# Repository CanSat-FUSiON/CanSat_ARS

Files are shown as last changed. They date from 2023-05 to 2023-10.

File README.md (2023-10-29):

# CanSat_ARS-1.00

**Present Version : ARS-1.00**
誰かが個人単位でリファクタリングやデバッグしたら+0.01，ミッションぐるみで大型アップデートをしたら+1.00して小数部切り捨て．
編集したら更新すること
ToDoはここに記すと管理しやすい：https://github.com/orgs/CanSat-FUSiON/projects/5/views/1?layout=board

## ディレクトリ説明
|ディレクトリ名|説明|
|----|----|
|Design-Data|CanSatの設計データが格納されています．CanSatを自分の好きなようにアレンジする場合にはこちらのディレクトリを操作してください．|
|Operation-Guide|CanSatの保守運用に関するデータが格納されています．機器の組立てと運用を行う場合はこのディレクトリのみ覗けば大丈夫です．|

## 命名規則
ディレクトリ名は原則，頭文字のみ大文字(複数単語は"-"で接続)
ファイル名は小文字統一

マークダウンファイルはGitHub直下のみ`README.md`とし(本ファイル)，それ以下の階層ではファイルの内容に従って命名する．
例）`./Design-Data/Hardware/`におけるハードウェア機器の構成を説明するためのマークダウンファイルは`ハードウェア機器の構成.md`

## コーディング規則
開発に使う言語としてpythonを用いる．
ただし，OBCの変更や機能拡張に伴い要求が変わる場合その限りではない．
pythonにおけるコーディング規約として，[pep8](https://pep8-ja.readthedocs.io/ja/latest/)にしたがう．

## ブランチの使い方
大会の出場の途中などで頻繁な更新が想定される際は，`main`の代理となる別な開発ブランチを設けること．
その場合，審査書提出後や，大会期間が終了時など，変更が安定した時点で開発ブランチを`main`にマージすること．
例）Mission4の開発期間中→`dev-m4`などと名付け暫定的な`main`の代わりとして用いる．

## コミットメッセージ
コミットメッセージは以下の4種類から適切なものを選び **(作業対象)+(: )+(作業分類)+(半角スペース)+(作業内容)** と書く．
例）`zero: Add telecomunication driver`
|作業分類|説明|
|----|-----|
|fix|バグ修正|
|add|新規(ファイル)機能追加|
|update|機能修正(バグではない)|
|remove|削除(ファイル)|

※（参考）https://qiita.com/itosho/items/9565c6ad2ffc24c09364

## ライセンス
This repository is released under the MIT License, see LICENSE.txt.

このリポジトリはMITライセンスのもとで公開されている． 'LISENCE.txt'を参照．

## バージョン管理
|Ver.|内容|
|----|----|
|1.00|Mission2終了時点の完成形CanSat|
|||

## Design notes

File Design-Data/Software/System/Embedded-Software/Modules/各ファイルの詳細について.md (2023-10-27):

# Modules
CanSatの組み込みソフトウェアに使うModuleをまとめるディレクトリです。

## ファイルの説明
|ファイル名|説明|
|----|-----|
|camerarun.py|画像処理走行のクラスを定義しているファイル|
|communication.py|LoRa通信のクラスを定義しているファイル|
|gpsrunner.py|GPS走行のクラスを定義しているファイル|
|landingdetecter.py|着地判定のクラスを定義しているファイル|
|logs.py|あらゆるログを記録するためのクラスを定義しているファイル|
|longsleep.py|走行前のスリープを制御するクラスを定義しているファイル|
|mdlreddetect.py|赤色を検出する関数が定義されているファイル|
|motor.py|CanSatの走行を統括するクラスが定義されているファイル|
|runpattern.py|CanSatの走行パターンの関数を定義しているファイル|
|sensor.py|GPSや9軸センサなどの値を取得するクラスを定義しているファイル|
|stack.py|様々な方法でスタックを判定するクラスが定義されているファイル|
|step.py|GPS走行中、ループの中で、それぞれの判定が設定されたインターバル通りに実行されるよう計測するクラスを定義したファイル|
|sleeptime.txt|スリープの設定時間が記録されるテキストファイル|

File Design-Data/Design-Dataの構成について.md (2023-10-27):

# Design-Data

ARSモデルの設計データを記載する．
現在のディレクトリは以下のように分けられる．
|フォルダ名|説明|
|----|----|
|Mechanic|機体構造や試験によって判明した物理特性に関するデータを記載する．|
|Hardware|組み込みハードウェア分野についての設計データを集める．マイコンとセンサ，アクチュエータなどの電気的な接続やPCBデータなど．|
|Software|組み込みソフトウェアや画像処理分野の設計データを集める．|

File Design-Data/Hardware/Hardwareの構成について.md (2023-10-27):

# Hardware
FUSiONのCanSat Model ARS系統のハードウェア設計

## ピンアサイン


更新する際は[こちらのスプレッドシート](https://docs.google.com/spreadsheets/d/1eQN7OE-Z9ALaf2SgiwYws5UZOM_eGH8C7UVVMnbFOFw/edit#gid=0)をコピーしてスクリーンショットを添付して下さい  

## 部品リスト
用いた代表的な部品は以下の通り．
具体的な型番などは別ファイルで示す．
|部品名|用途|
|----|----|
|温湿度気圧センサ|気温・気圧から高度を測定|
|9軸センサ|自身の向きの確認．及び転倒やスタック検知|
|GPSセンサ|自身の座標の確認．|
|モーター|走行やスタックからの脱出．|

以下に詳細な部品リストを表示する

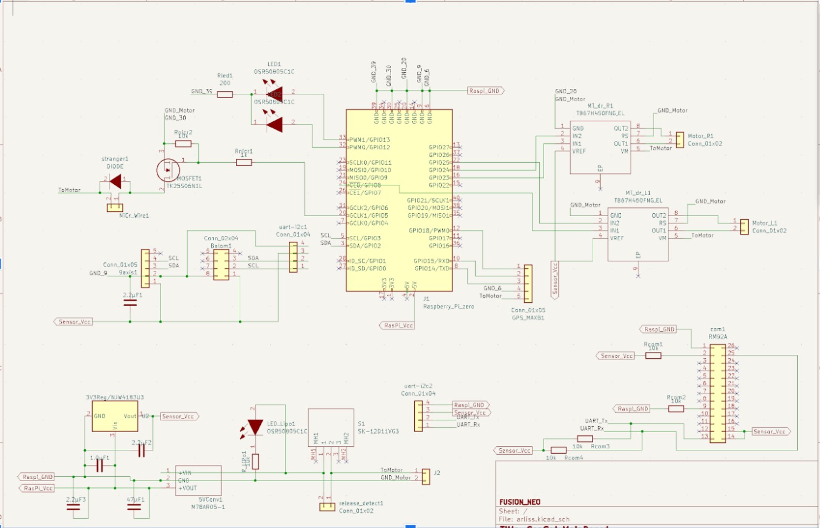
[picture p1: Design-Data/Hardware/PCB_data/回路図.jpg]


|名前|型番|用途|数|
|----|----|----|----|
|||||

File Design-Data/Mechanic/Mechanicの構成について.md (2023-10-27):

# Mechanic
CanSatをなす部品のCadデータを格納されている。
".f3z"はダウンロードした上でfusion360内でファイルを選び展開する。

## ディレクトリ/ファイルの説明
|ディレクトリ/ファイル名|説明|
|----|-----|
|buildup.f3z|すべての部品が統合されているcadファイル|
|parts|部品のcadデータが格納されたファイル|

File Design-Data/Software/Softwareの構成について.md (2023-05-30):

# Software
組込みソフトウェア，その他画像処理などのソフトウェアに関して記す．

## ディレクトリ説明
|ディレクトリ名|説明|
|----|-----|
|System|最終的に使用したプログラム|
|Interface-Test|複数の機能を連続して動かす際のテストに使うプログラム|
|Function-Test|機能単位のテストに使うプログラム|
|Component-Test|部品単位のテストに使うプログラム|

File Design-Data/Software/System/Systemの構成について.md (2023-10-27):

# System
マザーボードに組み込むデータと通信に使うデータを格納している。

## ディレクトリ/ファイルの説明
|ディレクトリ/ファイル名|説明|
|----|-----|
|Embedded-software|マザーボードに組み込むプログラムが格納されたディレクトリ|
|LoRa-software|通信機器に組み込むプログラムが格納されたディレクトリ|

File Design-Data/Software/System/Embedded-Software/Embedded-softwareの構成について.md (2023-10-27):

# Embedded-software
走行で実際に使用するプログラムとそれらのModuleをまとめるディレクトリです。
このディレクトリ上でmain.pyを実行すると、統合された組み込みプログラムが実行され、
打ち上げ開始からの一連の動作が始まります。

## ディレクトリ/ファイルの説明
|ディレクトリ/ファイル名|説明|
|----|-----|
|Modules|各種クラスを定義したプログラムをまとめたディレクトリ|
|main.py|mainとして実行するプログラム|

## 注意
- sleeptime.txtの数値を確認する。
    - この数値が-1だと、すぐに落下判定のフェーズに入る。実行からsleepする時間はこの数値を変更することで設定できる。
    - 数値はmain.pyの実行ごとに変更されていくため、毎回チェックする必要がある。
- 今後追加します。

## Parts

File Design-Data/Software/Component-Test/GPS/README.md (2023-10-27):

# 説明
GPS用の動作試験用プログラムです．

## 使い方
terminalからGPSモジュールをインストールしてください
>$pip install GPS3

UARTピン(TX:GPIO14，RX:GPIO15)に接続したのち，GPS.pyを実行してください．

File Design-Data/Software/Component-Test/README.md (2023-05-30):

# Component-Test

組込みモジュールそれぞれのテストをするためのディレクトリです．

## 組み込み部品リスト
|部品名|型番号|
|----|----|
|温湿度気圧センサ|[LPS25HB](https://akizukidenshi.com/catalog/g/gK-13460/)|
|9軸センサ|[BNO055](https://akizukidenshi.com/catalog/g/gK-16996/)|
|GNSSモジュール|[現行版](https://akizukidenshi.com/catalog/g/gK-13849/)|
|通信モジュール|[RM-92A](https://www.green-house.co.jp/products/rm-92as/)|

# ファイル説明
|ファイル名|説明|
|----|----|
|lps25hb_data.py|温湿度気圧センサlps25hbからそれぞれの情報を取得するためのプログラム|
|bno055_data.py|9軸センサbno055からそれぞれの軸のデータを取得するためのプログラム|
|maxb_data.py|GNSSモジュールから3次元座標と時刻を取得するためのプログラム|

# 関連ライブラリ
|ライブラリ名|説明|
|----|----|
|LPS25HB.py|LPS25HB動作用のライブラリ|
|adafruit_bno055.py|adafruit社製BNO055動作用ライブラリ|
|......|......|

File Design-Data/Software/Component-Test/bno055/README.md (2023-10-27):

# 説明
bno055.pyを書き込んだ後に，bno055TEST.pyを動作してください．

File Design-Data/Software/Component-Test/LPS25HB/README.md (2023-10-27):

# 説明
気温・気圧センサであるLPS25HBの動作プログラムです．
LPS25HB.pyというモジュールを書き込み，LPS25HBTEST.pyで動作させてください．

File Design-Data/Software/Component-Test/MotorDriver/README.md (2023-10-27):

# 説明
モーターの試運転用プログラムです．

## ピンアサイン
右前転|25
右後転|8
左前転|23
左後転|24

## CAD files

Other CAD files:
Design-Data/Hardware/PCB_data/pico_greenhouse/LIB_PICO/PICO/Allegro/pico.psm
Design-Data/Hardware/PCB_data/pico_greenhouse/LIB_PICO/PICO/DEHDL/pico/chips/chips.prt
Design-Data/Mechanic/Assemblies/GYSFDMAXB.f3d
Design-Data/Mechanic/Assemblies/bearingholder.f3d
Design-Data/Mechanic/Assemblies/coupling.f3d
Design-Data/Mechanic/Assemblies/motorholder.f3d
Design-Data/Mechanic/Assemblies/plate1.f3d
Design-Data/Mechanic/Assemblies/plate2.f3d
Design-Data/Mechanic/Assemblies/plate3.f3d
Design-Data/Mechanic/Assemblies/ripobattery.f3d
Design-Data/Mechanic/Assemblies/shaft.f3d
Design-Data/Mechanic/Assemblies/shaftholder.f3d
Design-Data/Mechanic/Assemblies/spacer_20mm.f3d
Design-Data/Mechanic/Assemblies/spacer_30mm.f3d
Design-Data/Mechanic/Assemblies/stabilizer.f3d
Design-Data/Mechanic/Assemblies/substrate1.f3d
Design-Data/Mechanic/Assemblies/substrate2.f3d
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

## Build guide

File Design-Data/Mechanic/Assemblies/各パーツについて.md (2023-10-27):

# Parts
CanSatをなす部品が個別に格納されている。
拡張子が".f3d"のためダウンロードした上、fusion360で展開する。

## ディレクトリ/ファイルの説明

以下にファイル名と内容についてまとめた。プリント欄が〇となっているものは3Dプリンターで制作するもの、✕となっているものは購入・発注・製作するものである。

|ファイル名|説明|プリントの有無|データシート|購入リンク|
|----|----|----|----|----|
|plate1.f3d|CanSat上層部のデータ|〇|-|-|
|plate2.f3d|CanSat中層部のデータ|〇|-|-|
|plate3.f3d|CanSat下層部のデータ|〇|-|-|
|substrate1.f3d|raspberryPi 0を載せた基板データ|✕|[here](./../../../Hardware/)|-|
|substrate2.f3d|9軸センサーを載せた基板データ|✕|[here](./../../../Hardware/)|-|
|substrate3.f3d|RaspberryPi Picoを載せた基板データ|✕|[here](./../../../Hardware/)|-|
|GYSFDMAXB.f3d|GPSセンサーのデータ|✕|[here](https://akizukidenshi.com/download/ds/akizuki/AE-GPS_manual_r1.06_s.pdf)|[here](https://akizukidenshi.com/catalog/g/gK-13849/)*|
|tire.f3d|タイヤのデータ|〇|-|-|
|wheel.f3d|ホイール部分のデータ|〇|-|-|
|shaft.f3d|シャフトのデータ|✕|-|-|
|shaftholder.f3d|シャフトとホイールをつなげるシャフトホルダーのデータ|✕|[here](https://jp.misumi-ec.com/pdf/fa/2018/p1_269_001_202106.pdf)|[here](https://jp.misumi-ec.com/vona2/detail/110300010440/?ProductCode=STHRB5)|
|bearingholder.f3d|シャフトを通すベアリングを中層プレートに締結させる部品のデータ|〇|-|-|
|coupling.f3d|シャフトとモーターを接続するカップリングのデータ()|✕|[here](https://jp.misumi-ec.com/pdf/fa/2018/p1_1139_003_202106.pdf)|[here](https://jp.misumi-ec.com/vona2/detail/110300125670/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)|
|motorholder.f3d|モーターを中層に締結させる部品のデータ|✕|-|-|
|ripobattery.f3d|リポバッテリーのデータ|✕|[here](https://www.amazon.co.jp/YOWOO-%E3%83%90%E3%83%83%E3%83%86%E3%83%AA%E3%83%BC-2600mAh-%E3%83%AA%E3%83%9D%E3%83%90%E3%83%83%E3%83%86%E3%83%AA%E3%83%BC-RC%E8%BB%8A%E3%8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)|[here](https://www.amazon.co.jp/YOWOO-%E3%83%90%E3%83%83%E3%83%86%E3%83%AA%E3%83%BC-2600mAh-%E3%83%AA%E3%83%9D%E3%83%90%E3%83%83%E3%83%86%E3%83%AA%E3%83%BC-RC%E8%BB%8A%E3%8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)|
|spacer_20mm.f3d|中層と上層をつなぐスペーサーのデータ|✕|-|-|
|spacer_30mm.f3d|下層と中層をつなぐスペーサーのデータ|✕|-|-|
|stabilizer.f3d|スタビライザーとしてコンベックステープを取り付ける部品のデータ|〇|-|-|

*元の危機はすでに販売停止になっており、リンクは後継機のリンクとなっている。

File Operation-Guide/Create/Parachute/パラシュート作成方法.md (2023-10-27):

# Parachute
パラシュートの部品と設計図をまとめたディレクトリです.

## パラシュートの部品/材質
|使用する部品|使用する材質|サイズ|
|----|-----|---|
|パラフォイル|ナイロンタフタ/リップストップナイロン|1500mm四方|
|パラコード|ナイロン紐(テグス)|各700mm|
|ハトメ|真鍮製|直径8mm|

## パラシュートの設計図
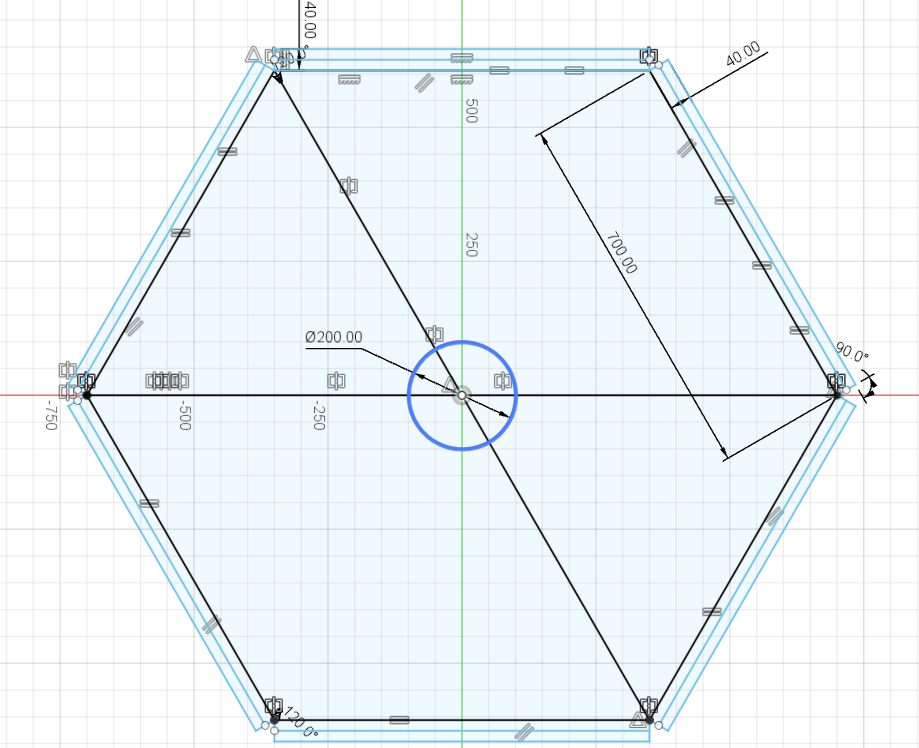
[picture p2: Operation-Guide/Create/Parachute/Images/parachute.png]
parachute


## 製作行程
1. 青細線の通りに布を切り出す.
2. 黒線に一致するように正六角形の端の長方形を二回折り返して縫う.
3. 青太線の通りに中心を切り落とす.
4. 正六角形の各頂点にハトメにあったサイズの穴(8mm)を開け、ハトメで補強する.  

※パラシュートの中央部に穴を開けるのは、風に煽られて横流しにされるのを軽減するためである.穴が大きいほど風に流されにくくなるが、その分落下速度は上昇するため、注意が必要.

## 布の選び方
### 色
パラシュートの落下時や落下後に機体を捜索しやすくするため、視認性の高い色を採用する.  
例えば、空中にいるときに青系統の色は見つけにくいし、砂地であれば黄色に近い色は見えにくくなってしまう.  
したがって、2022年度ARLISSでは、赤色のパラシュートを作成した.
### 素材
傘に使われるナイロンタフタや、テント等のアウトドア用品に用いられるリップストップナイロンを強く勧める.  
軽量で破れにくいことや、パラシュートの減速機構としての能力を十分に発揮できる.

## 紐の選び方
### ナイロン紐にも複数の種類がある
- 金剛打ち
- 16打ち
- 8打ち
- テグス  
上から丈夫である一方重量が大きくなっている.
重量制限などを考慮して選択してほしい.  
ARLISS2022では、テグスを用いてパラコードを作成した.  
    金剛打ち  
      
    16打ち  
      
    8打ち  
      
    テグス  
      
    [参考紐](https://www.taisei-mfg.co.jp/lesson.html)  
    [参考テグス](https://tsuri-labo.jp/word/24268#google_vignette)
    
## 紐の結び方
### ハトメとパラシュートの結び方
1. ハトメにラインを2回通し,輪を作る.  
  
1. 本線にラインを4〜5回程度巻き付ける.  
  
1. ラインを1.で作った輪に通す.  
  
1. ゆっくりと締め込む.  
  
[参考](https://www.seaguar.ne.jp/knot/parts/parts_5.html)  
### パラシュートの紐のまとめ方
1. パラシュートのテグスを6本まとめる.  
1. 8の字結びしてガムテープで固定する.
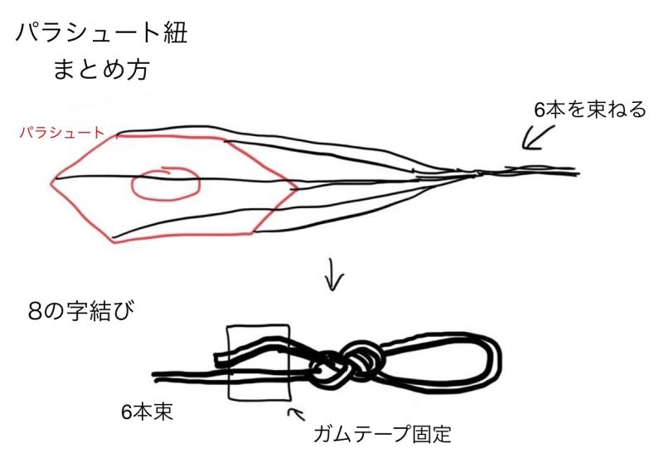
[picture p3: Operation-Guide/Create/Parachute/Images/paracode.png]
paracode
  

## 畳み方
### パラコードを一つに集めるように畳む
1. パラコードが集まるように半分に4回折りたたむ
2. 半分に折りたたんで、その上に紐を折り曲げて置く
3. コードを一緒に包むようにして、もう一度半分に折りたたむ
4. さらに折りたたんで一回巻いて完成  

パラシュート折りたたみ方  
[参考](http://joujaku-pc-club.blog.jp/archives/5920767.html)

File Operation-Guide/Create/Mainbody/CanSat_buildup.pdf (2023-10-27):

# CanSat 組み上げ書

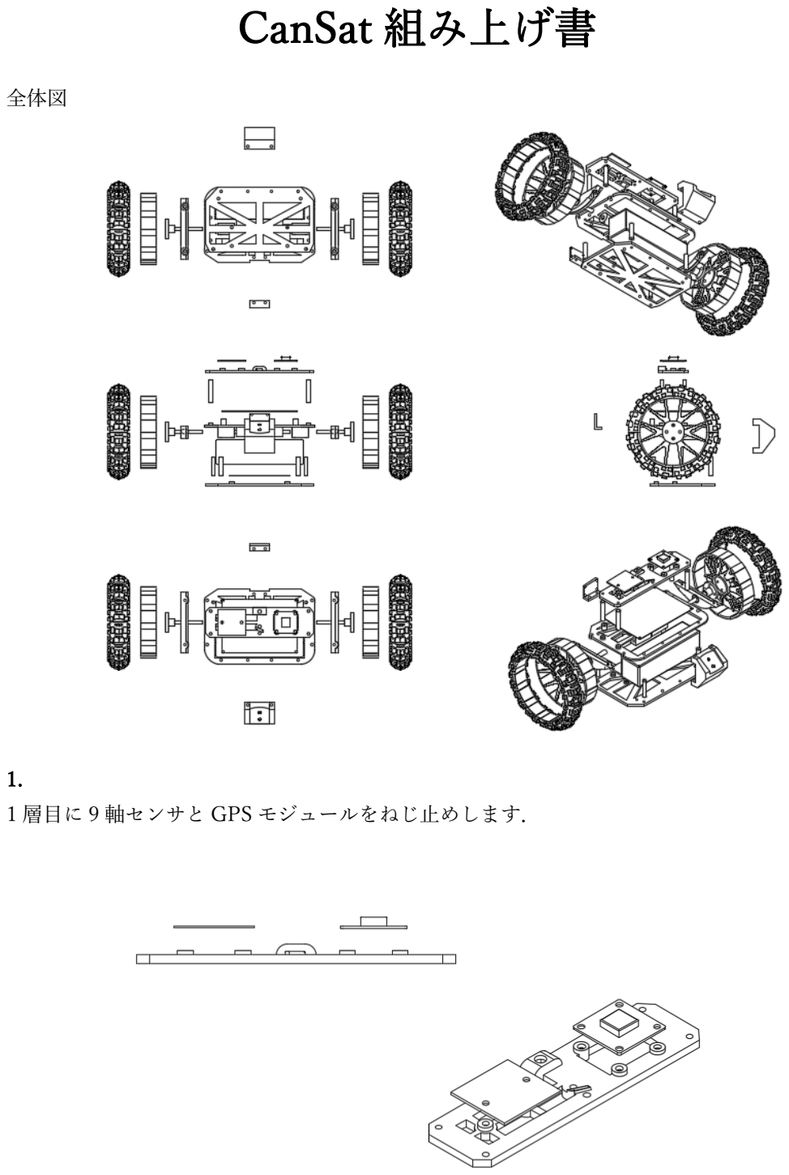
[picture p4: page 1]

全体図

1.
1 層目に 9 軸センサと GPS モジュールをねじ止めします．

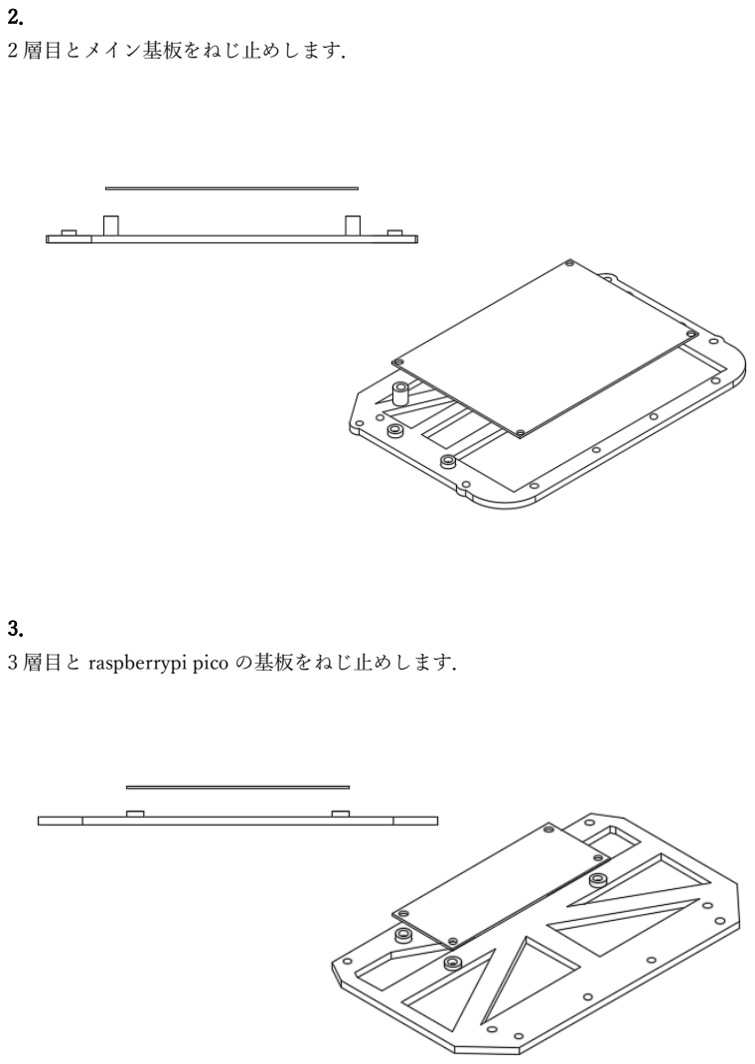
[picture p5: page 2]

2．
2 層目とメイン基板をねじ止めします．

3．
3 層目と raspberrypi pico の基板をねじ止めします．

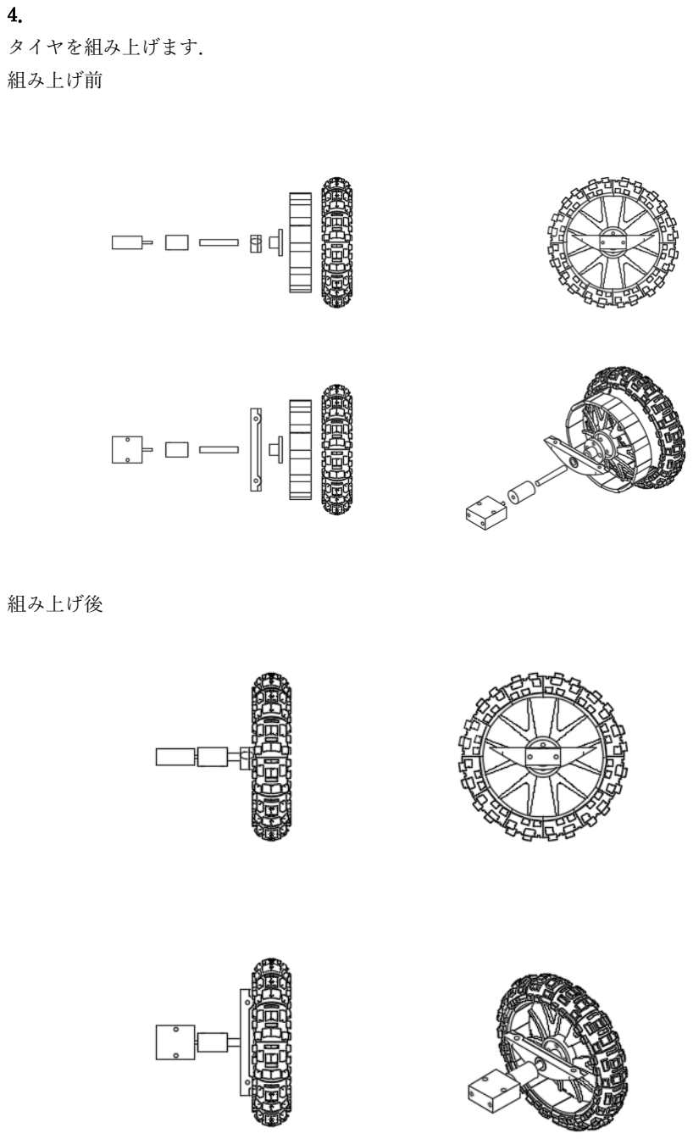
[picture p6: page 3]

4．
タイヤを組み上げます．
組み上げ前

組み上げ後

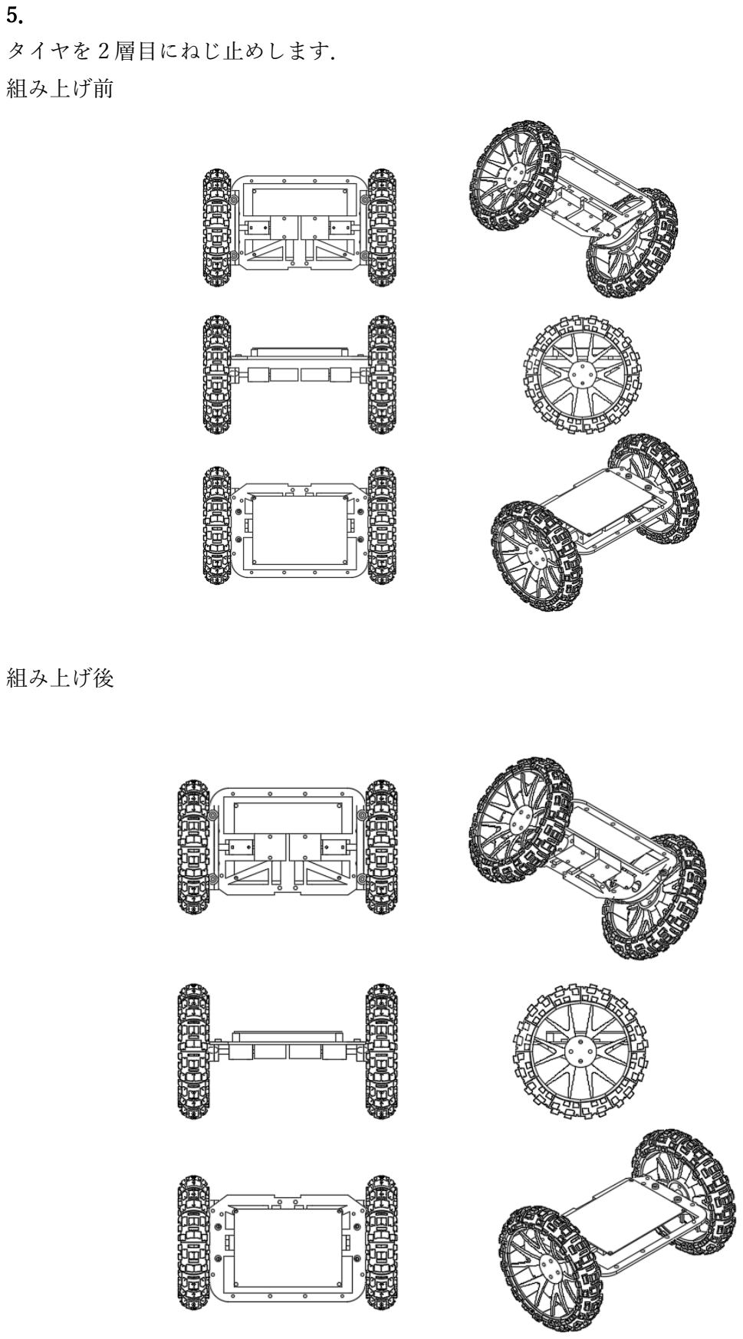
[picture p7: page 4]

5．
タイヤを 2 層目にねじ止めします．
組み上げ前

組み上げ後

6．
1 層目と 3 層目とリポバッテリーを 2 層目にスペーサーで止めます．

7．

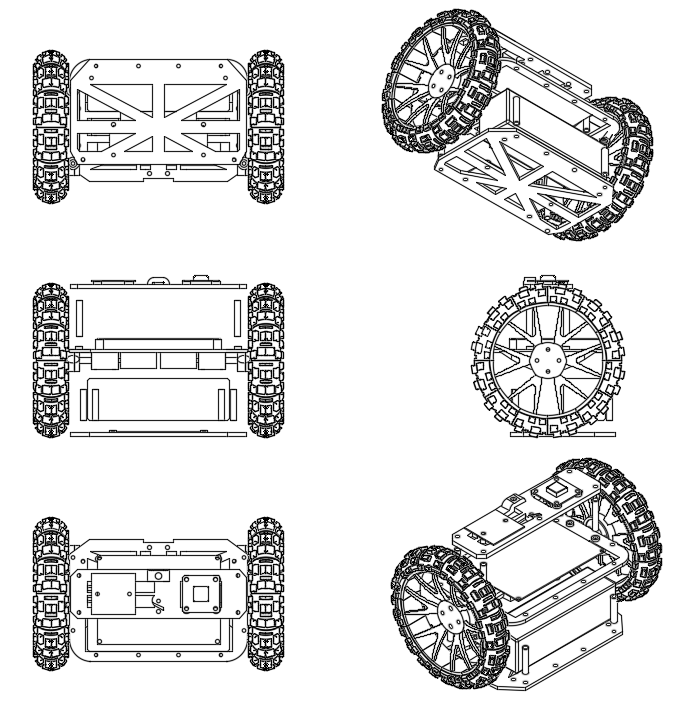
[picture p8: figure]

カメラ締結部とスタビライザーを結合します．

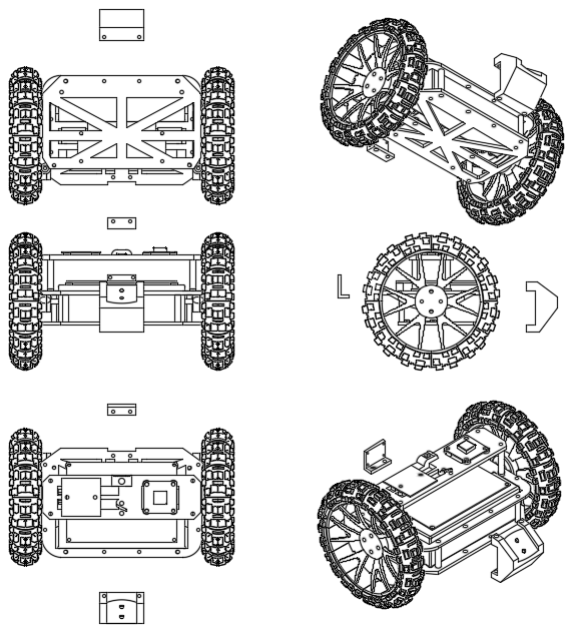
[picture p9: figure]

8．
完成です．

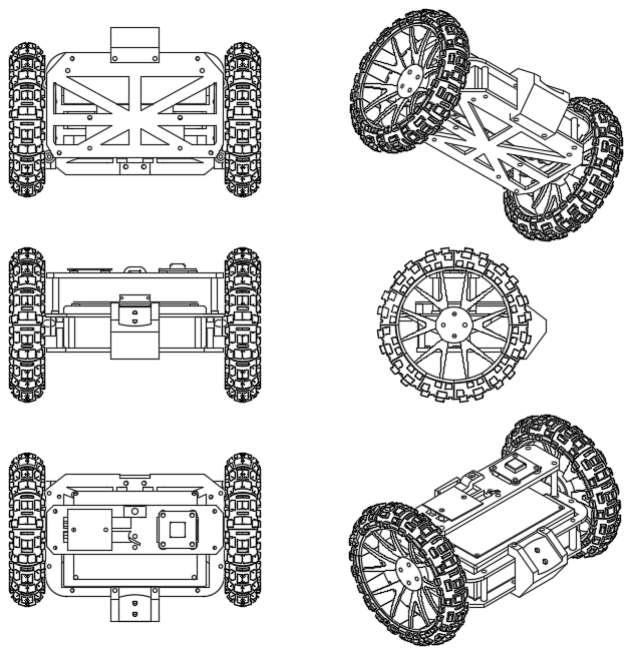
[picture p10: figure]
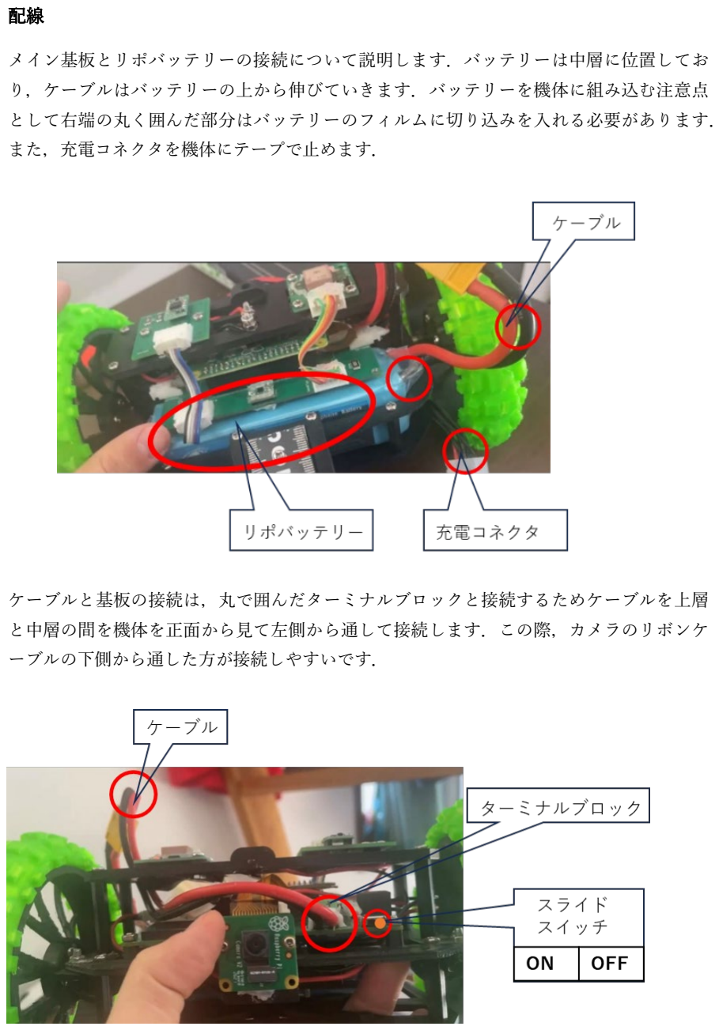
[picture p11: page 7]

配線
メイン基板とリポバッテリーの接続について説明します．バッテリーは中層に位置してお り，ケーブルはバッテリーの上から伸びていきます．バッテリーを機体に組み込む注意点 として右端の丸く囲んだ部分はバッテリーのフィルムに切り込みを入れる必要があります． また，充電コネクタを機体にテープで止めます．

ケーブルと基板の接続は，丸で囲んだターミナルブロックと接続するためケーブルを上層 と中層の間を機体を正面から見て左側から通して接続します．この際，カメラのリボンケ ーブルの下側から通した方が接続しやすいです．

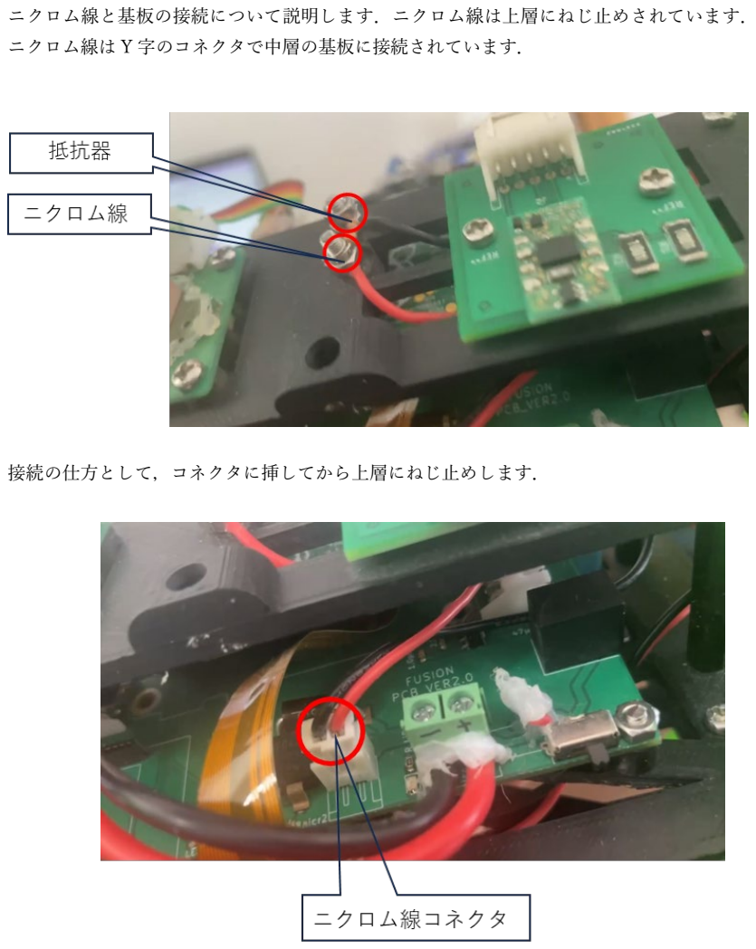
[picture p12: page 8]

ニクロム線と基板の接続について説明します．ニクロム線は上層にねじ止めされています． ニクロム線は Y 字のコネクタで中層の基板に接続されています．

接続の仕方として，コネクタに挿してから上層にねじ止めします．

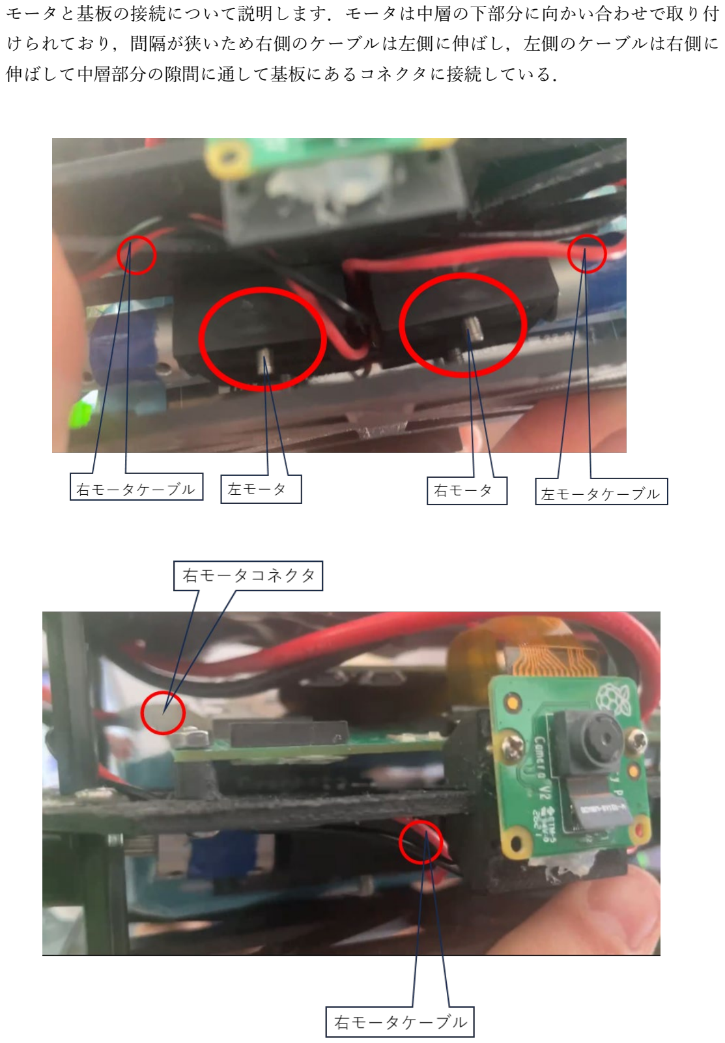
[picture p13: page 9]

モータと基板の接続について説明します．モータは中層の下部分に向かい合わせで取り付 けられており，間隔が狭いため右側のケーブルは左側に伸ばし，左側のケーブルは右側に 伸ばして中層部分の隙間に通して基板にあるコネクタに接続している．

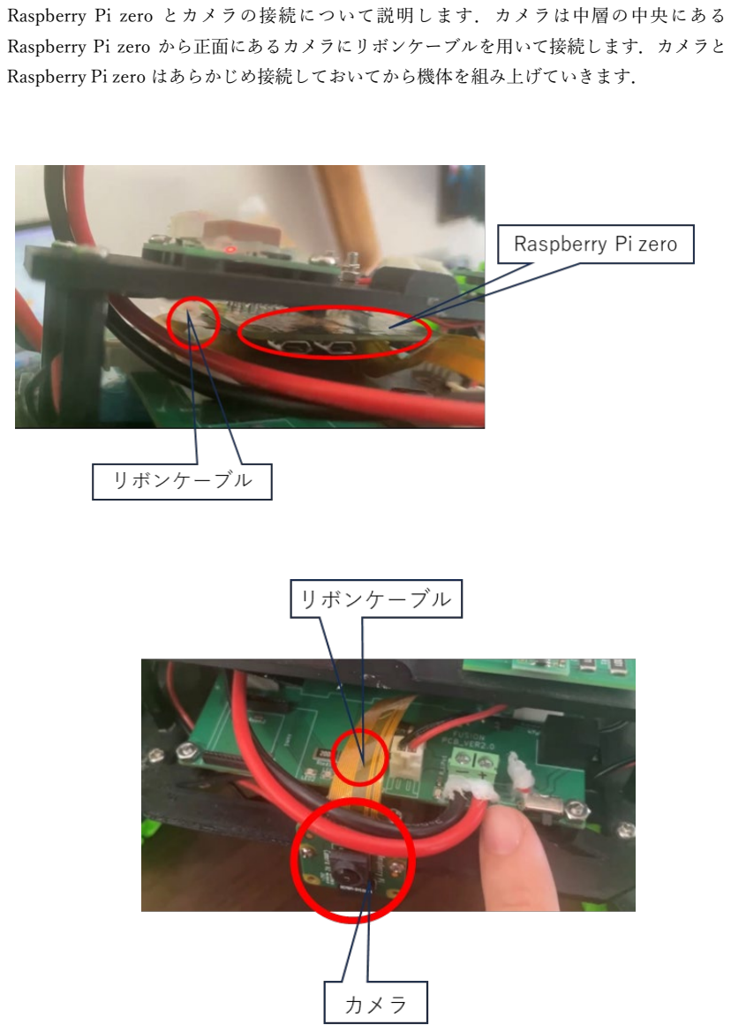
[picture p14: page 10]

Raspberry Pi zero とカメラの接続について説明します．カメラは中層の中央にある Raspberry Pi zero から正面にあるカメラにリボンケーブルを用いて接続します．カメラと Raspberry Pi zero はあらかじめ接続しておいてから機体を組み上げていきます．

それぞれの接続の順番としては，はじめにリボンケーブルを接続し，次に下層と中層を組 み上げた際にモータを基板と接続します．次に上層と接続する際にニクロム線と基板の接 続を行います．最後に電源ケーブルを接続します．電源ケーブルの接続の際の注意点とし て，スライドスイッチが OFF になっていることを確認してから接続してください．

上記の接続後に 9 軸センサ，GNSS センサをメインの基板と接続します．xh コネクタをそ れぞれのセンサと基板に接続する際の注意点として，9 軸センサは基板側とセンサ側で向 きが同じですが，GNSS センサは，基板側とセンサ側で向きが逆になります．

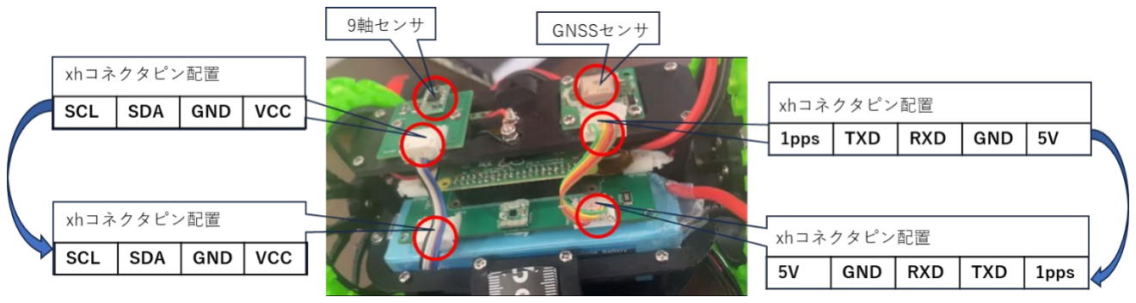
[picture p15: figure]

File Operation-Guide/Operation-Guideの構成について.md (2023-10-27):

# Operetion-Guide

このディレクトリ内に，Model-ARSの使用方法を記す．  
運用手順に限らず，組み立てや保守点検の仕方も記載する．
|フォルダ名|説明|
|----|----|
|Create|CanSatを作成する手順となる資料を格納している．|
|Operations-Control|CanSatの管制運用に関する資料を格納している．|

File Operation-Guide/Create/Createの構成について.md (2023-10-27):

# Create
Createには、CanSatを作成する手順となる資料を格納している。
構成は以下のようになっている。
|フォルダ名|説明|
|----|----|
|Envelope|エンベロープの作成方法についての資料を格納している．|
|Mainbody|機体の組み上げ方に関する資料を格納している．|
|Parachute|パラシュートの作成方法についての資料を格納している．|
|Communication|無線通信のセッティング方法についての資料を格納している．|

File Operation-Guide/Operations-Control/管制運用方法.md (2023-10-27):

# Operations-Control

## 無線の受信についてのトラブルシューティング
機体を受け渡し後，ダウンリンクをとれない場合には以下のことを確認・実行をする．

1．TeraTerm上でbaurateの確認を行う．

TeraTermを開き，baurateの設定を確認する．

baurateは 設定>>シリアルポートを開き，以下のような画面で115200に設定する．

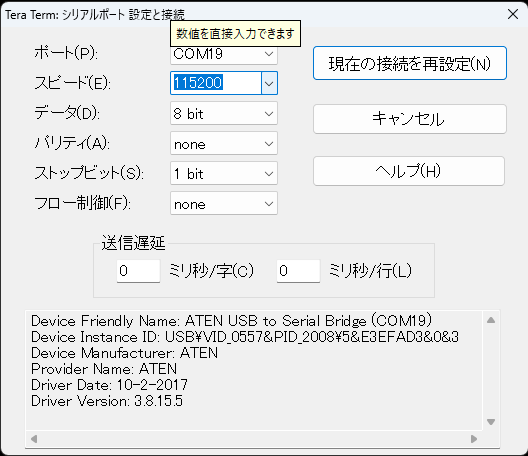
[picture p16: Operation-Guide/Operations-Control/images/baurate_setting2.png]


2．baurateを設定しなおしても動作しない場合はTeraTermの再起動を行う．

　一度Teratermを閉じたのち，１で説明したのと同じように再設定する．

3．それでも動作しない場合は，地上局側を再度設定しなおす必要がある．（設定については[Component/RM92Aを参照](../../Design-Data/Software/Component-Test/RM92A)）

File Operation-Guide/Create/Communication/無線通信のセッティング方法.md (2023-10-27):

# 説明
RM92Aは地上局に機体情報をダウンリンクさせるために用いる無線モジュールです．
本プログラムでは機体側にRaspberry Pi Pico，地上局側にNUCLEO-F303K8を使用しています．
無線通信のセッティングに関わるデータは[こちら](./../../../Design-Data/Software/System/LoRa-Software/RM92A/)に格納されています.

# セッティング
RM92Aは使用前にセッティングが必要になります．
## セッティング方法
地上局にRM92Aを乗せた状態で*setting_rm92a.NUCLEO_F303K8.bin*ファイルを書き込んでください．
pcにつないぎTeraTermを開いた状態でトグルスイッチを押したらセッティング画面へ移行できます．（TeraTermのbaurateは115200に変更してください）
## セッティングの内容
セッティングする内容については，RM92Aの販売元であるGreenHouseの[pdf](https://www.green-house.co.jp/book/iot-wireless/SimpleMACstd92A-92C_instruction%20manual-rev2.9.15.pdf)をご参照ください．

基本的なセッティングでは
|コマンド|指定する値（機体側）|指定する値（地上局側）|
|----|----|----|
|a|24|24|
|c|0|1|
|d|65535|0|
|e|0|1|
|i|0|0|
|t|0|0|

上のように書き込みが終わったらxで変更内容を保存してください．

# 使い方
## 機体側
**機体側**はpythonファイルを2つ書き込んでください．
*FUSiON_RM92A.py*は自作ライブラリになってます．
*RM92A_TEST.py*が実際に動かしてもらうプログラムです．

## 地上局側
**地上局側**はmbedのオンライン開発環境となります．[公式ページ](https://os.mbed.com/)にアクセスし，アカウント登録してください．
その後以下のように3つのファイル全てを記述し，ビルドしてください．

### ビルドのやり方
上のリンクからアカウント作成，ログインしたのち，以下のようにFile>New>Mbed Progectと進みます．
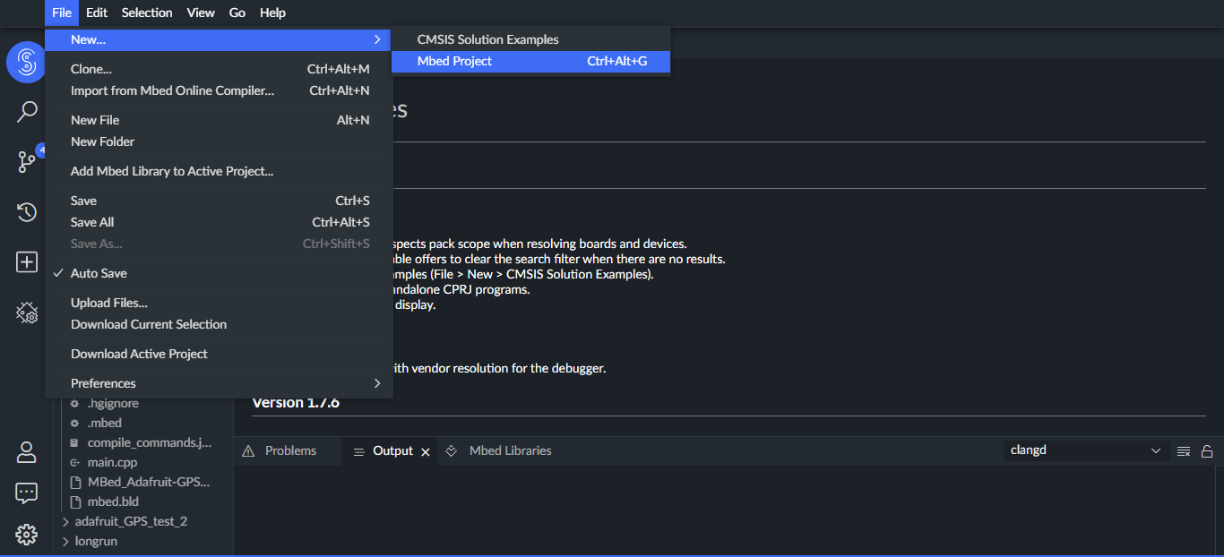
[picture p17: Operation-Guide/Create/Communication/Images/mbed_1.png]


そうすると以下のような画面が出てくるため，**Example Projectをmbed2-example-blinky**に設定して新規プロジェクトを作成します．
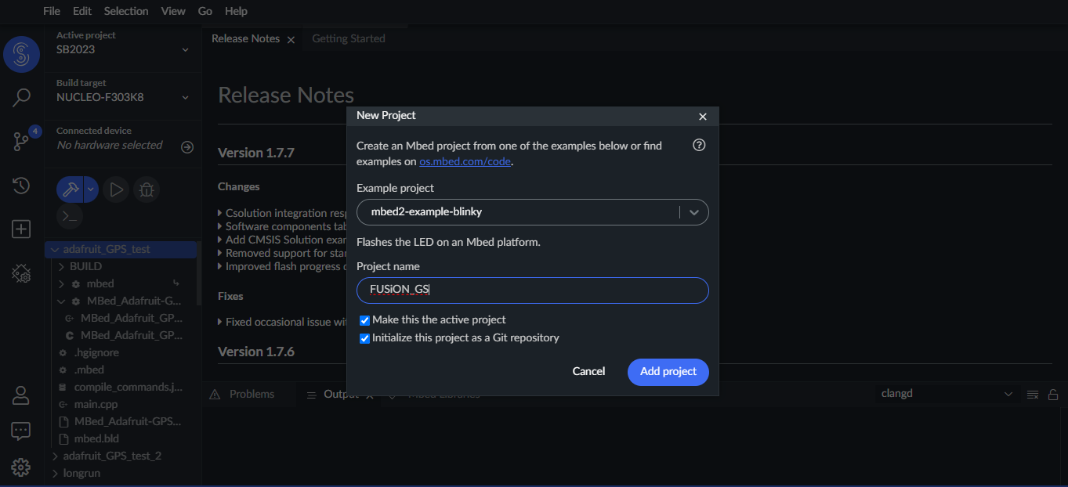
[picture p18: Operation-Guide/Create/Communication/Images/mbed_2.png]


次に以下のようにActive Projectの確認とBuild targetの設定を行います．
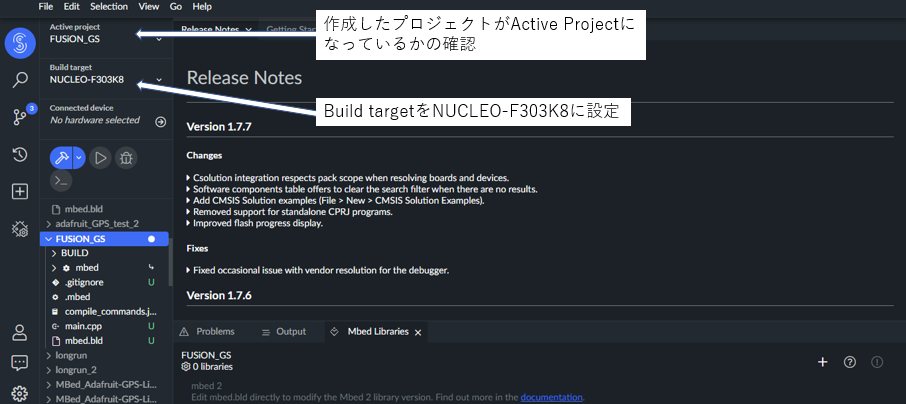
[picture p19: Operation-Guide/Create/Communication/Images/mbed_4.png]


設定が行えたらプロジェクトを右クリックし，新規ファイルを追加します．
ここに*main.cpp*，*FUSiON_RM92A.h*，*FUSiON_RM92A.cpp*を作成（コピペ）してください．
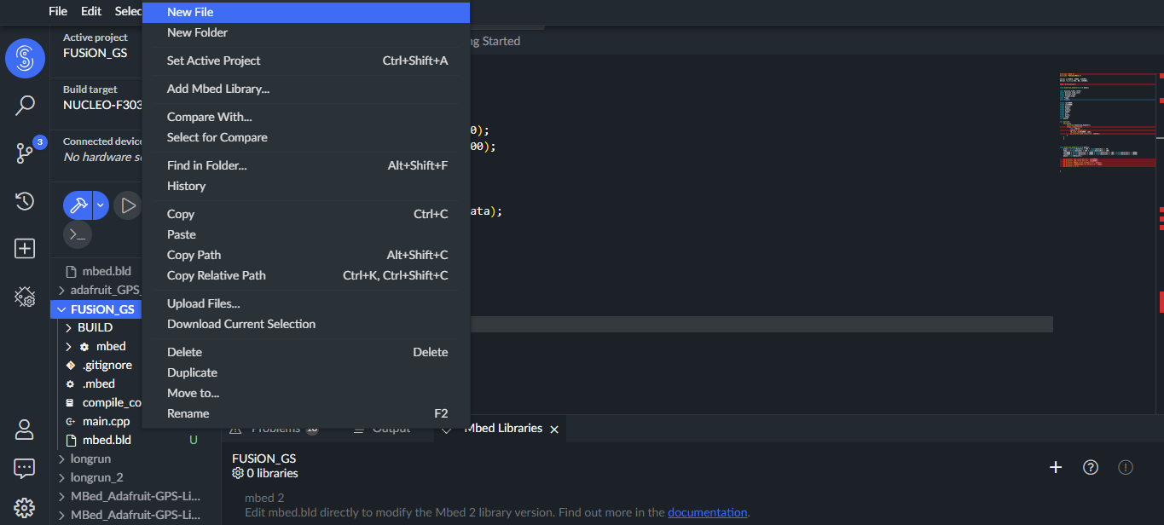
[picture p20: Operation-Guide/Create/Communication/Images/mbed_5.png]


記述が完了したらビルドを完了してください．
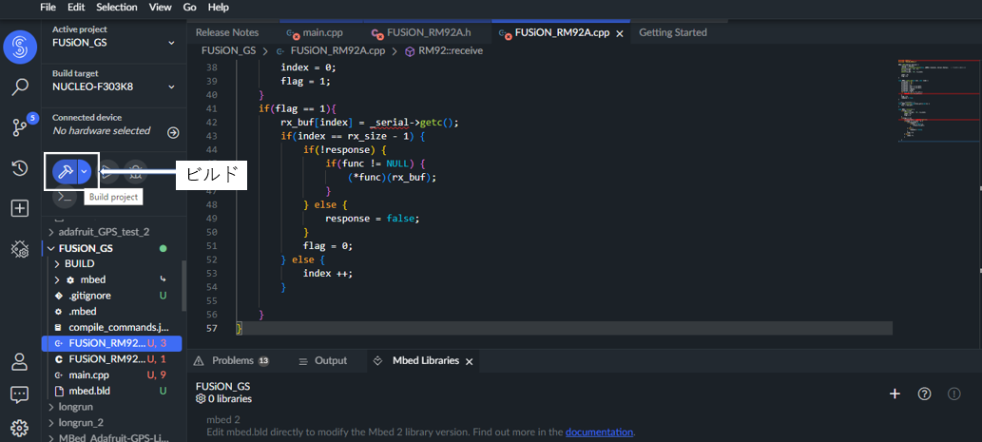
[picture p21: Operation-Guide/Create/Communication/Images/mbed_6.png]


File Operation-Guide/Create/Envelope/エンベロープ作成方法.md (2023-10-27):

# Envelope
エンベロープの部品と設計図をまとめたディレクトリです.

## エンベロープの部品/材質
|使用する部品|使用する材質|サイズ|
|----|-----|---|
|エンベロープ|PPクラフトシート+アルミホイル+紙やすり+コンベックステープ+ハトメ|　|
|溶断用ひも|テグス|100mm|
|固定用ひも|ナイロン紐|直径3mm|
|その他|針金・ビニルテープ||

## エンベロープの概念図
以下に設計図を記載する.
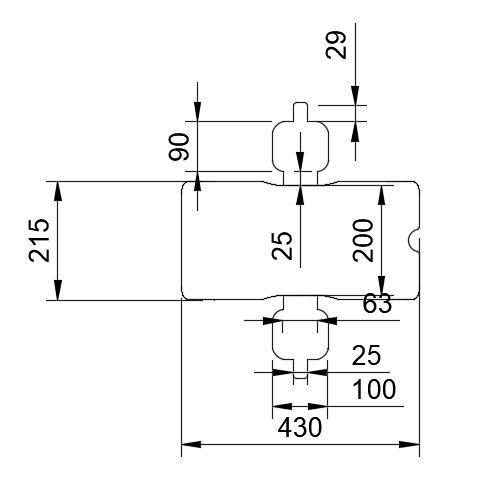
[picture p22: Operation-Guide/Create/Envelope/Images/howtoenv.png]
envelope設計図


## 素材の選び方
まず、PPクラフトシートについて、適度な反発力を持ち合わせていると考える.反発力がありすぎると、キャリア内部で変形し、上手く放出できないことがある.一方反発力が足りない場合、溶断したのちにCanSatがエンベロープから脱出できない恐れがある.

また、エンベロープが開放により確実に開くようにエンベロープ内にコンベックステープをとりつけた.

次に、紙やすりについて、タイヤが滑らないようにするためにエンベロープのタイヤが乗る部分に粗目の紙やすりをボンドで貼り付ける.

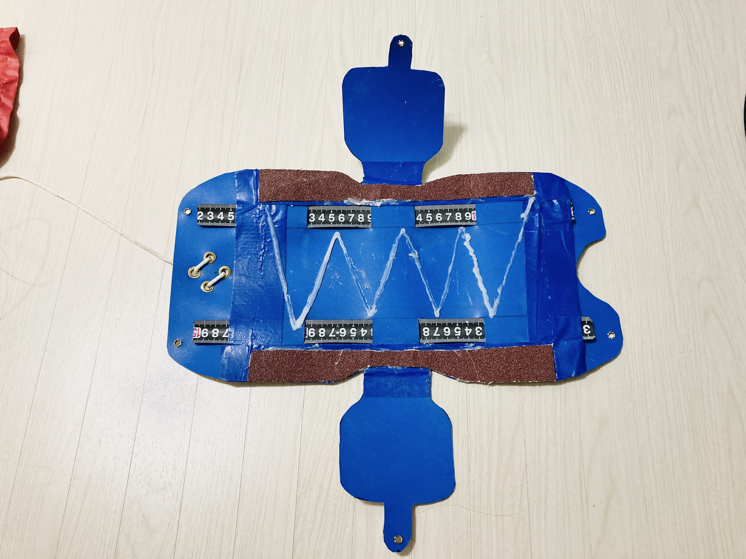
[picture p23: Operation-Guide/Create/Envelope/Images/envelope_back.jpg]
envelope裏面


次に、不必要な電磁的干渉を防ぐため、エンベロープにアルミホイルテープを巻き電磁遮蔽を行った.

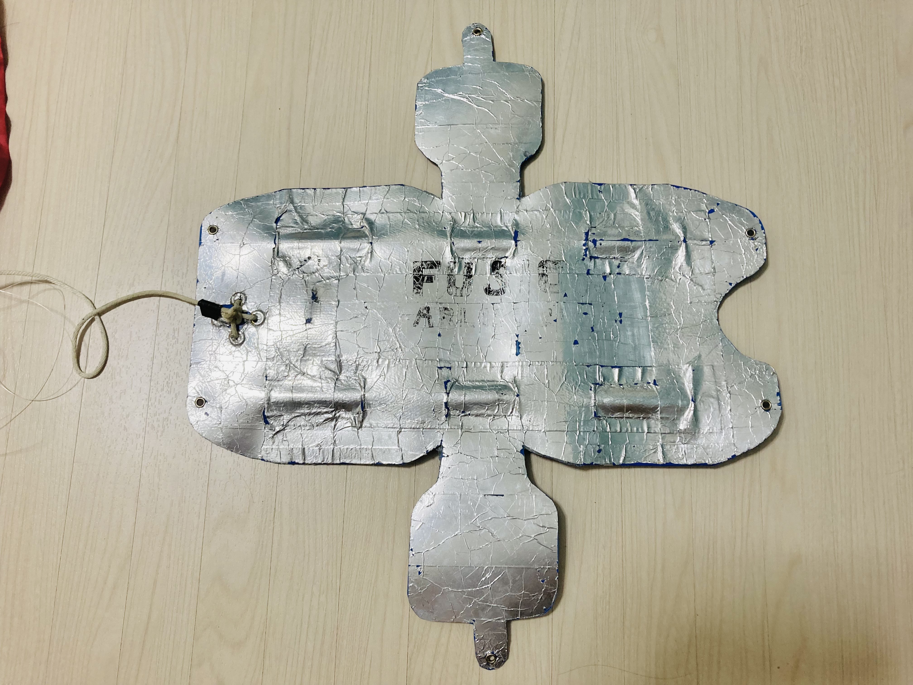
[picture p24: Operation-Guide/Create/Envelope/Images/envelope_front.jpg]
envelope表面


最後に紐について、まずナイロン紐はエンベロープとパラシュートを接続するために用い、テグスは機体を覆うためにエンベロープを固定し、着地後に焼き切るための紐である.

## 紐の結び方
### エンベロープとパラシュートの固定
以下に、エンベロープに接続する紐の結び方・パラシュートの紐とエンベロープの紐の接続について描いたものが以下の図である.
なお、赤の線がエンベロープ側の紐で、黒の線がパラシュートの紐を表し、パラシュートの紐の結び方については[パラシュートの作成方法.md](Design-Data/Mechanic/Parachute/パラシュート作成方法.md)を確認していただきたい.
また、ラインやパラシュート用のロープを通す穴に全てハトメを付けて強化した.
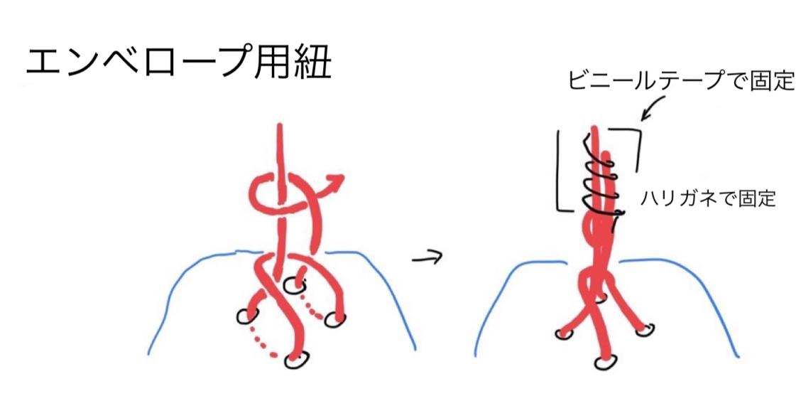
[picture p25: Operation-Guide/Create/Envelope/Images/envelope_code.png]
parashute_code

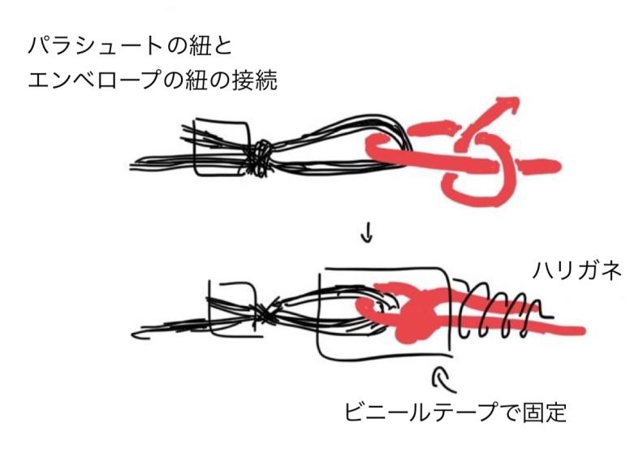
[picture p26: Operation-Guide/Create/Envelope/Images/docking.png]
envelope_code


### エンベロープによるCanSatのカバー
また、エンベロープを円柱状に固定する際のテグスの結び方を以下に示す.
一枚目のようにエンベロープの穴に番号を振る.
なお、以下の写真二枚目の赤の線がテグスを表す.
1. エンベロープ内側からタイヤ側面側の穴(①)にテグスを通す.テグスを穴に通す前に、テグス溶断用のニクロム線を通してから穴に通すようにすること.
2. パラシュートの紐と接続している側の長辺の穴に通す.
3. もう一方の辺に穴を通してテグスを結ぶ.なお、テグスは固結びで結ぶが、ほどけないように念入りに確認してほしい.
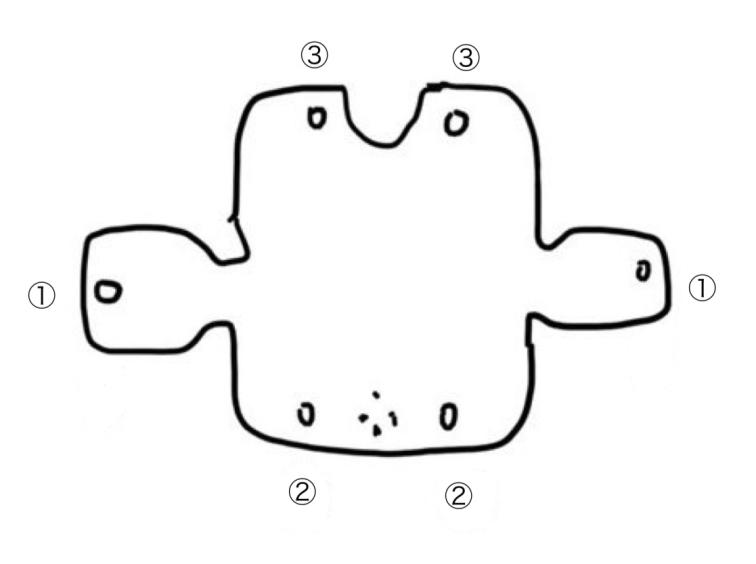
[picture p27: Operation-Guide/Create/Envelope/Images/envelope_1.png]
envelope_code

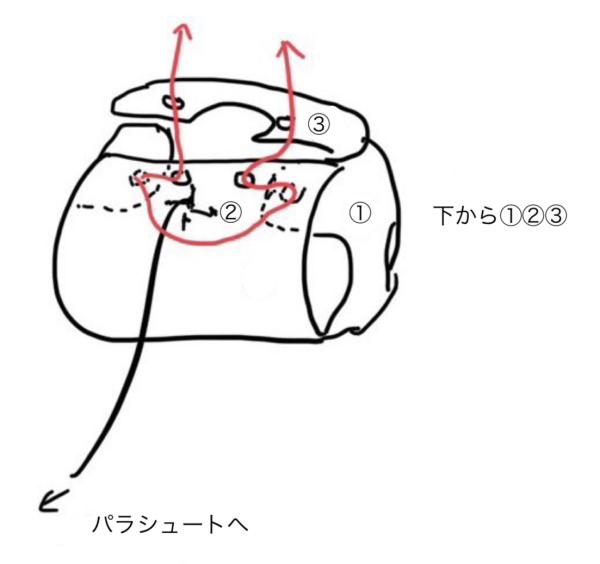
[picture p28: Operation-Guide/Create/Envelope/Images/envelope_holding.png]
envelope_code


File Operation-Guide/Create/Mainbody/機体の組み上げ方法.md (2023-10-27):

# 説明
CanSatの機体の組み上げに関する構造物のCadデータは[こちら](./../../../Design-Data/Mechanic/)に格納されています。
[CanSat_buidup.pdf](./CanSat_buidup.pdf)に組み上げの手順が記されています。

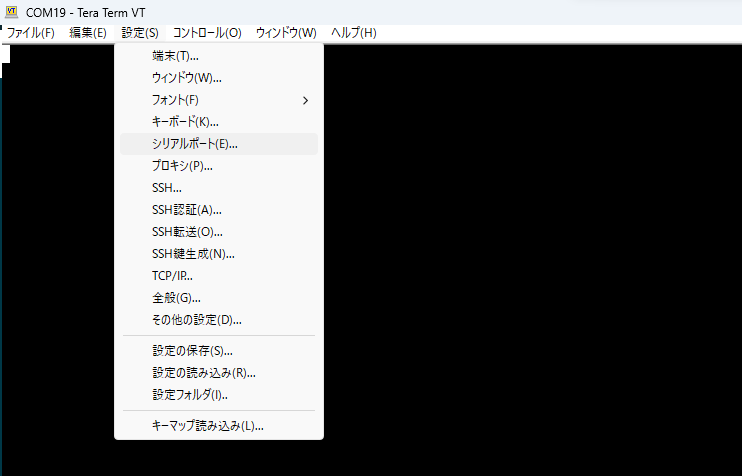
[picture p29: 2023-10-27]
Operation-Guide/Operations-Control/images/baurate_setting1.png

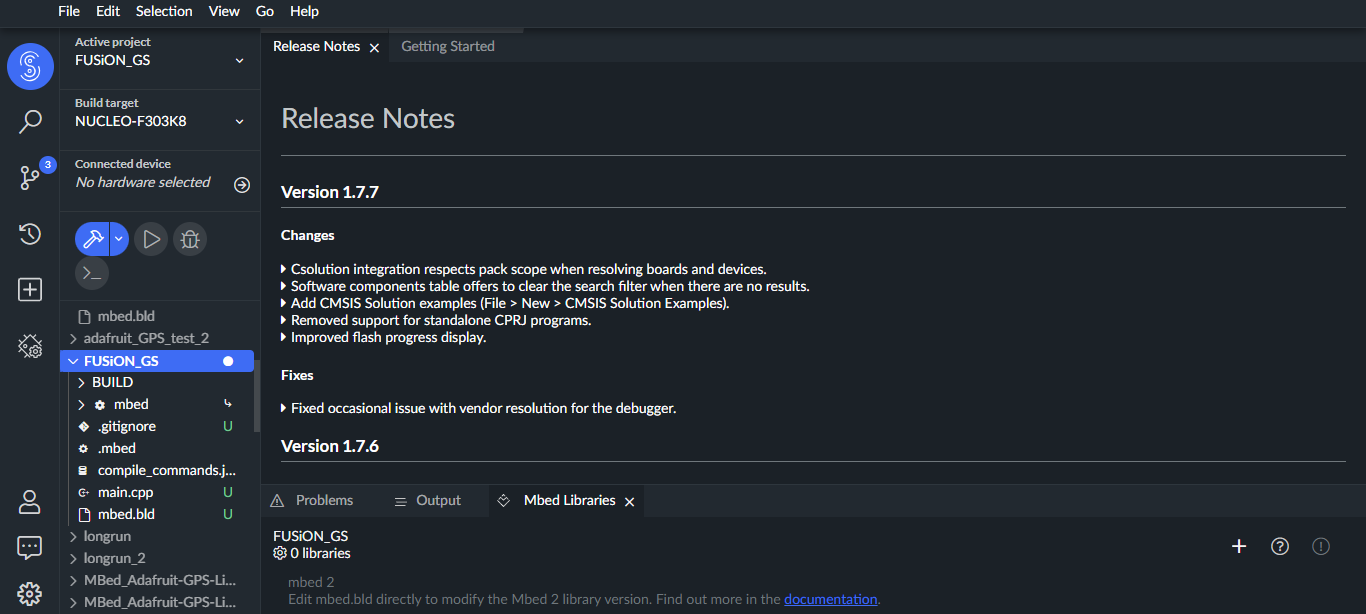
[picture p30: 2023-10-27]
Operation-Guide/Create/Communication/Images/mbed_3.png

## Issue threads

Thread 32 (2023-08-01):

issureとプルリクエストをリンクさせる方法を調べる。

KazumaKato, 2023-08-01:

KazumaKato, 2023-08-06:
調べました。こちらをご覧ください。
@MayaAbe @SeigaMatsuura @KyoheiShiota @22kyugi
[github_wiki](https://docs.github.com/ja/issues/tracking-your-work-with-issues/linking-a-pull-request-to-an-issue)

Pull Request の右のタブから Development で該当の issure を選択して紐づける漢字みたいです。確認よろしく。（自分のやつは紐づけ完了しました。）

Closed 2023-08-06.

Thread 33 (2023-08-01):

CanSat-FUSiON の Organization のメンバー整理

KazumaKato, 2023-08-01:

KazumaKato, 2023-08-06:
@MayaAbe @SeigaMatsuura @KyoheiShiota

hidehideno-ri
LilKoke11
mayk-skice2012
okapiiiiiii
ririastro

大体メンバーから外したのですが、だれか判別つかない人が上の5人です。消してよさそうな人を教えてください。

KazumaKato, 2023-08-07:
ririastroは消していい。
LilKoke11は不明。

Closed 2023-08-14.

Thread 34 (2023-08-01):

ケンシンから9軸の基板データを受け取る

KazumaKato, 2023-08-01:

KazumaKato, 2023-08-06:
量基板のデータはケンシンがUSBをなくしていたので復元不可能とのことでした。
さて、どうしましょうか？

KazumaKato, 2023-08-07:
星河が作っている基板のデータがあるにはあるが、Kicadを使っていないことが難点。
星河はイーグルを使用。RM92Aはピンのサイズが違うので、部品データがない可能性あり。

まとめると、kicadに部品のデータが入っていれば、星河のを見ながらKicadで作り直してもらうことは可能。（ケンシンに依頼してみる。）

KazumaKato, 2023-08-07:
9軸について

基板のサイズが機体にあうように作り直すのはすこし難しい。基板の実物のサイズ感さえわかれば再現は可能。（ケンシンに確認）

KazumaKato, 2023-08-14:
あべまなど、基板（9軸と地上局）のデータを持っている人とkicadを使える人に復元してもらう

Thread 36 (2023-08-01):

GitHubの使い方記事を読む

MayaAbe, 2023-08-01:
これ読む
https://github.com/CanSat-FUSiON/CanSat_Fundamentals/blob/main/teach_04_EnvironmentBuilding/01_Git_and_VisualStudioCode.md

KyoheiShiota, 2023-08-01:
https://github.com/CanSat-FUSiON/CanSat_Fundamentals/blob/main/teach_04_EnvironmentBuilding/01_Git_and_VisualStudioCode.md

MayaAbe, 2023-08-01:
@KazumaKato
終わったらこんな感じでメンションして報告しよう

KazumaKato, 2023-08-07:
@@KazumaKato
読み終わりました。

22kyugi, 2023-08-07:
@KazumaKato
読み終わりました

tkt08, 2023-08-07:
@KazumaKato
読みました

Closed 2023-08-07.

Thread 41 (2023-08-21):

運用の仕方

KazumaKato, 2023-08-21:

KazumaKato, 2023-08-21:
エンベロープへの包み方・紐の通し方 ⇒ @22kyugi
パラシュートの畳み方 ⇒ @22kyugi
電波の受信 ⇒ @SeigaMatsuura

KazumaKato, 2023-08-30:
@MayaAbe が写真を送り、それを @22kyugi がみてまとめる。

KazumaKato, 2023-08-30:
Operations-Controlに追加する。 @SeigaMatsuura @22kyugi

KazumaKato, 2023-09-06:
@SeigaMatsuura 今手元に無線機器がないため、画像を載せられていない。手元に来るのは10月の頭なので、今の時点では画像なしでもわかるレベルで作り上げ、画像載せるだけの状態にしておく。無線のセッティングも同様。
@22kyugi どのように配線をするのかの手順や注意点、画像の部品の補足などを加え、ボリュームアップする必要がある。

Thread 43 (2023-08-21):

プログラムやソフトウェアのセッティング

MayaAbe, 2023-08-21:

KazumaKato, 2023-08-21:
いまのところ、インストールすべきライブラリなどの洗い出しが十分ではないので、次に実際に使うタイミングで必要になるものをメモり、セッティングのファイルを作成する。
@MayaAbe @22kyugi @SeigaMatsuura
プログラムで使うパラメータは @KazumaKato が教える。

KazumaKato, 2023-09-06:
@MayaAbe 実際にARLISSで使っていたラズパイを用いて必要なライブラリなどの情報を抜き取るなどは可能。情報の抜き出し方を調べるところまで来週までにやる。

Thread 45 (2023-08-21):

エンベロープの作り方

KazumaKato, 2023-08-21:

KazumaKato, 2023-08-30:
島と連絡をとれていてかける状態ではある。（まだ書けていない）
9月4日までにとりあえず作る。

KyoheiShiota, 2023-09-06:
パラシュートの紐の接続、テグスの通し方、サイズ、紙やすりの貼り方

KazumaKato, 2023-09-12:
・画像には登場していないが→消す
・島君の絵にかいてる文字を上から修正
・紐のすみわけ
・パラシュートとエンベロープの紐の説明
・設計図デザインから図面

・作業おわったらoperation guideに移行

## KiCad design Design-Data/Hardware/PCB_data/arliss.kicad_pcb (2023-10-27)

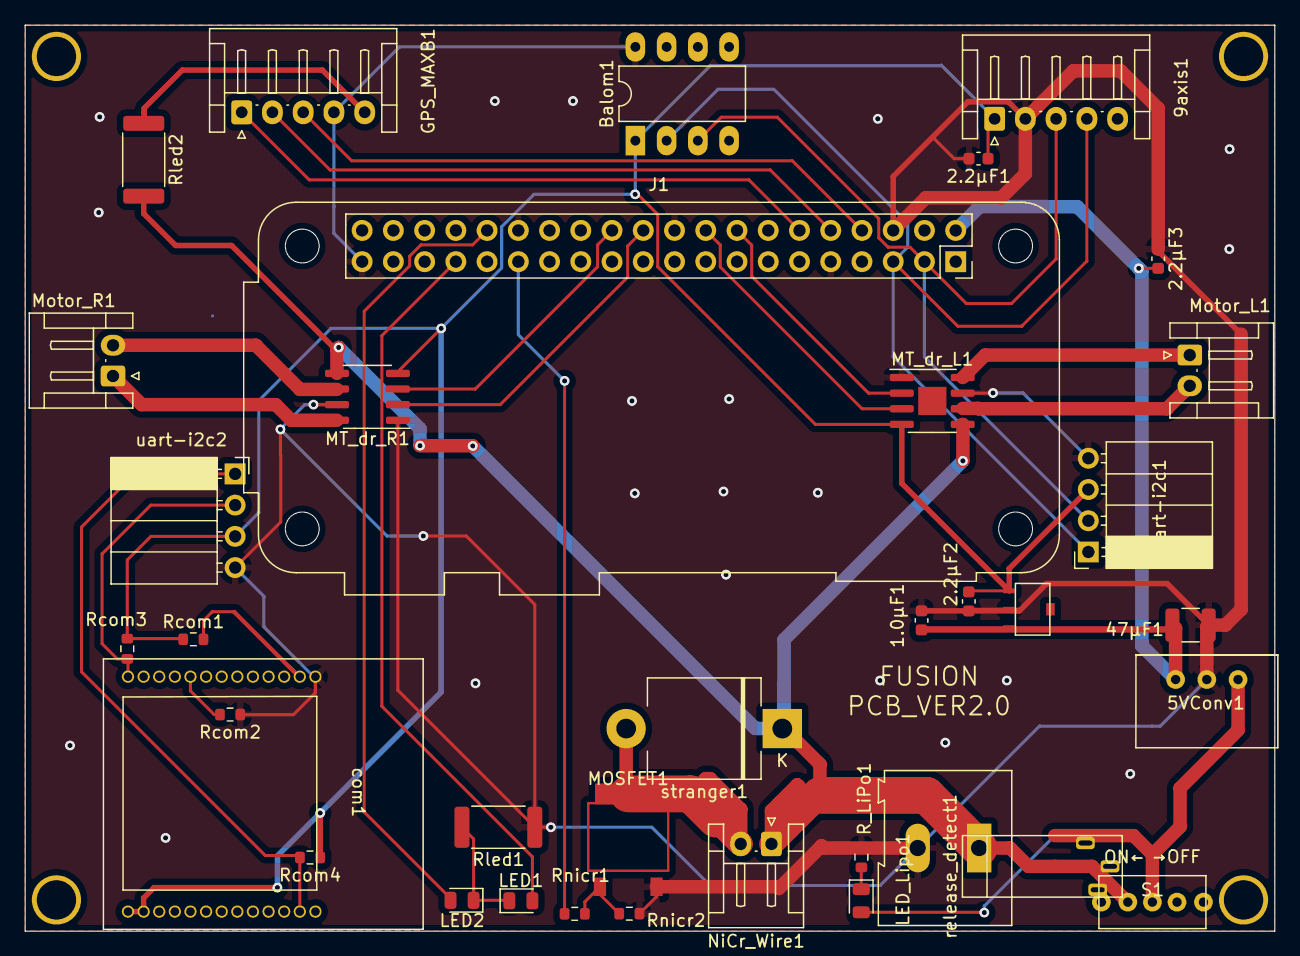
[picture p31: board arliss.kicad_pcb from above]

Board: 2 copper layers, 101.6 x 73.7 mm, 36 parts (0 on the bottom side), 30 nets.

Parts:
1.0μF1, 2.2μF1, 2.2μF2, 2.2μF3: C; C_0603_1608Metric
5VConv1: M78AR05-1
9axis1: Conn_01x05; JST_EH_S5B-EH_1x05_P2.50mm_Horizontal
47μF1: C; C_1210_3225Metric
Balom1: Conn_02x04; DIP-8_W7.62mm_LongPads
GPS_MAXB1: Conn_01x05; JST_EH_S5B-EH_1x05_P2.50mm_Horizontal
J1: Raspberry_Pi_zero; Raspberry_Pi_Zero_Socketed_THT_FaceDown_MountingHoles
J2: Conn_01x02; TerminalBlock_Altech_AK300-2_P5.00mm
LED1, LED2: OSR50805C1C; LED_0805_2012Metric
LED_Lipo1: OSR50805C1C; LED_0805_2012Metric
MOSFET1: TK25S06N1L; TK25s06N1L
MT_dr_L1: TB67H450FNG,EL; HSOP-8-1EP_3.9x4.9mm_P1.27mm_EP2.3x2.3mm
MT_dr_R1: TB67H450FNG,EL; HSOP-8-1EP_3.9x4.9mm_P1.27mm_EP2.3x2.3mm
Motor_L1: Conn_01x02; JST_EH_S2B-EH_1x02_P2.50mm_Horizontal
Motor_R1: Conn_01x02; JST_EH_S2B-EH_1x02_P2.50mm_Horizontal
NiCr_Wire1: Conn_01x02; JST_EH_S2B-EH_1x02_P2.50mm_Horizontal
R_LiPo1: 10k; R_0603_1608Metric
Rcom1, Rcom2, Rcom3, Rcom4: 10k; R_0603_1608Metric
Rled1, Rled2: 200; R_2512_6332Metric
Rnicr1: 1k; R_0603_1608Metric
Rnicr2: 10k; R_0603_1608Metric
S1: SK-12D11VG3
U2: 3V3Reg/NJW4183U3; NJW4183U3-33B
com1: RM92A; RM-92A
release_detect1: Conn_01x02; Release_Sensor
stranger1: DIODE; D_5KPW_P12.70mm_Horizontal
uart-i2c1, uart-i2c2: Conn_01x04; PinSocket_1x04_P2.54mm_Horizontal

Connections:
/SCL: 9axis1.4, Balom1.2, J1.5 (SCL/GPIO3), uart-i2c1.1
/SDA: 9axis1.3, Balom1.3, J1.3 (SDA/GPIO2), uart-i2c1.2
/ToMotor: J2.1, MT_dr_L1.5 (VM), MT_dr_R1.5 (VM), NiCr_Wire1.2, Rled2.2, release_detect1.1, stranger1.2 (A)
/UART_Rx: Rcom4.2, com1.25, uart-i2c2.1
/UART_Tx: Rcom3.2, com1.13, uart-i2c2.2
unnamed: 5VConv1.1 (+VIN), LED_Lipo1.2, release_detect1.2
unnamed: GPS_MAXB1.1, J1.12 (GPIO18/PWM0)
unnamed: GPS_MAXB1.2, J1.10 (GPIO15/RXD)
unnamed: GPS_MAXB1.3, J1.8 (GPIO14/TXD)
unnamed: GPS_MAXB1.5, Rled2.1
unnamed: J1.16 (GPIO23), MT_dr_R1.3 (IN1)
unnamed: J1.18 (GPIO24), MT_dr_R1.2 (IN2)
unnamed: J1.22 (GPIO25), MT_dr_L1.2 (IN2)
unnamed: J1.24 (~CE0/GPIO8), MT_dr_L1.3 (IN1)
unnamed: J1.29 (GCLK1/GPIO5), Rnicr1.2
unnamed: J1.32 (PWM0/GPIO12), LED2.2
unnamed: J1.33 (PWM1/GPIO13), LED1.2
unnamed: LED1.1, LED2.1, Rled1.2
unnamed: LED_Lipo1.1, R_LiPo1.2
unnamed: MOSFET1.1, Rnicr1.1, Rnicr2.2
unnamed: MOSFET1.2, NiCr_Wire1.1, stranger1.1 (K)
unnamed: MT_dr_L1.6 (OUT1), Motor_L1.2
unnamed: MT_dr_L1.8 (OUT2), Motor_L1.1
unnamed: MT_dr_R1.6 (OUT1), Motor_R1.2
unnamed: MT_dr_R1.8 (OUT2), Motor_R1.1
unnamed: Rcom1.2, com1.2
unnamed: Rcom2.2, com1.9
RasPi_Vcc: 1.0μF1.2, 2.2μF3.2, 5VConv1.3 (+VOUT), 47μF1.2, J1.2 (5V), U2.3 (Vin)
Raspi_GND: 1.0μF1.1, 2.2μF1.2, 2.2μF2.1, 2.2μF3.1, 5VConv1.2 (GND), 9axis1.2, 47μF1.1, Balom1.8, GPS_MAXB1.4, J1.6 (GND), J1.9 (GND), J1.20 (GND), J1.30 (GND), J1.39 (GND), J2.2, MOSFET1.3, MT_dr_L1.1 (GND), MT_dr_L1.7 (RS), MT_dr_R1.1 (GND), MT_dr_R1.7 (RS), R_LiPo1.1, Rcom2.1, Rled1.1, Rnicr2.1, U2.2 (GND), com1.1, uart-i2c1.4, uart-i2c2.4
Sensor_Vcc: 2.2μF1.1, 2.2μF2.2, 9axis1.1, Balom1.1, MT_dr_L1.4 (VREF), MT_dr_R1.4 (VREF), Rcom1.1, Rcom3.1, Rcom4.1, U2.1 (Vout), com1.14, com1.15, uart-i2c1.3, uart-i2c2.3

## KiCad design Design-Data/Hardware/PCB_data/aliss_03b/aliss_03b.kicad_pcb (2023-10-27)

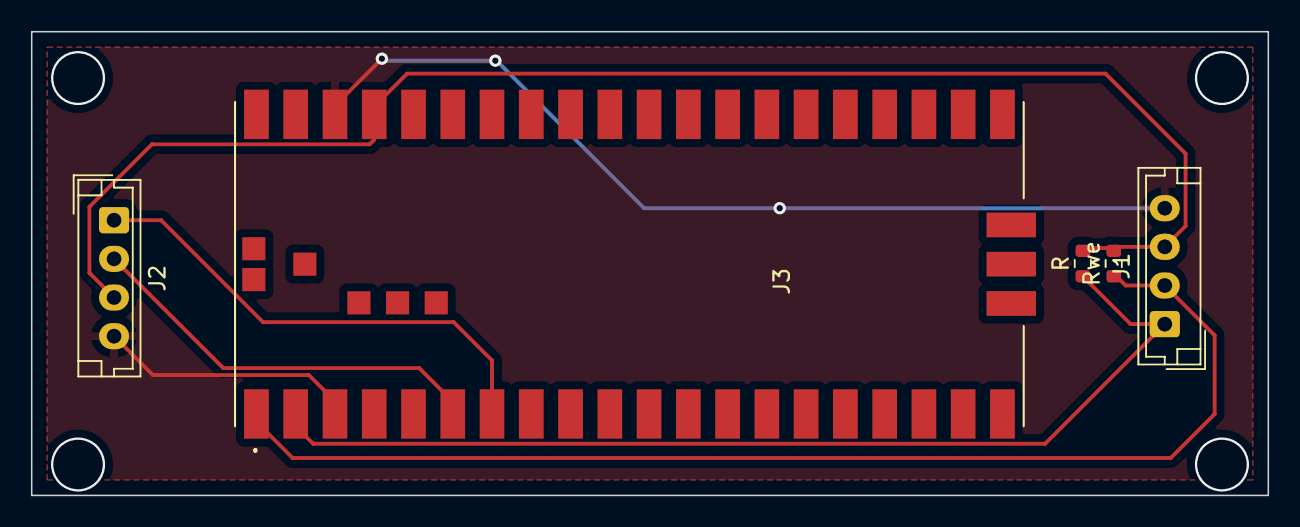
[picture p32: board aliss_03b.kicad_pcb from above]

Board: 2 copper layers, 80.0 x 30.0 mm, 5 parts (0 on the bottom side), 6 nets.

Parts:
J1, J2: Conn_01x04_Shielded; JST_EH_B4B-EH-A_1x04_P2.50mm_Vertical
J3: Conn_02x20_Counter_Clockwise; RaspberryPiPico
R: 10k; R_0603_1608Metric
Rwe: 10k; R_0603_1608Metric

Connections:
/3V3: J1.3, J2.3, J3.37, R.2, Rwe.2
/GND: J1.4, J2.4, J3.3, J3.38
/Rx: J2.2, J3.6
/SCL: J1.1, J3.2, R.1
/SDA: J1.2, J3.1, Rwe.1
/Tx: J2.1, J3.7

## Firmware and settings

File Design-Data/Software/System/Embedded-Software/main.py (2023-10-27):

from Modules.motor import Motor
from Modules.longsleep import Longsleep
from Modules.step import Step
from Modules.camerarun import Camerarun
from Modules.logs import Logs
from Modules.stack import Stackrun
from Modules.stack import Gpsstack
from Modules.stack import Accstack
from Modules.communication import Communicator
from Modules.gpsrunner import Gpsrunner
from Modules.sensor import Sensor
from Modules.landingdetecter import Landingdetecter

from geopy.distance import geodesic
import os
import smbus
from itertools import count
import csv
from gps3 import gps3
from time import sleep
import RPi.GPIO as GPIO
import board
import adafruit_bno055
import math
from readline import set_completion_display_matches_hook
from socket import MSG_WAITALL
from tokenize import Double
from adafruit_extended_bus import ExtendedI2C as I2C
import Modules.runpattern as runpattern
import sys
sys.path.insert(4, '/home/pi/.local/lib/python3.7/site-packages')


# import LPS25HB
# import random
# import time
# import serial
# from multiprocessing.connection import wait
# import multiprocessing
# import datetime

# import picamera
# import picamera.array
# import cv2 as cv
# import numpy as np

runpattern.first()  # 起動時にモーターが回ってしまうことを防止


def main():
    try:
        runpattern.first()
        step = Step()  # Step(Class)のインスタンスを作成。あらゆるタイマーはこのインスタンスの値で条件分岐する。
        step.set_longsleep_steptime()  # longsleeptimeを現在時刻(起動時)に設定。
        gps_setting_socket = gps3.GPSDSocket()  # GPS情報をやり取りするインスタンスを作成。
        gps_setting_socket.connect()
        gps_setting_socket.watch()

        logs = Logs()  # Log(Class)のインスタンスを作成。あらゆるlogはこのインスタンスを通して書き込まれる。
        communication = Communicator(bus=smbus.SMBus(
            1), logclass=logs, gps_socket=gps_setting_socket, data_stream=gps3.DataStream())  # 通信をするためのCommunicator(Class)のインスタンスを作成。

        landingdetect = Landingdetecter(  # Landingdetecter(Class)のインスタンスを作成。
            time_limit=0, burn_time=10, hlist=[0, 1, 2, 3, 4])

        longsleep = Longsleep(file_name='sleeptime', encoding='UTF-8',  # Longsleep(Class)のインスタンスを作成。
                              fr_time=0, com_time=2400, ld_time=1200, pt_time=10)

        sensor = Sensor(i2c=I2C(1), sensor=adafruit_bno055.BNO055_I2C(I2C(1)), gps_socket=gps_setting_socket,  # Sensor(Class)のインスタンスを作成。
                        data_stream=gps3.DataStream(), lastval=0xFFFF, offset_mag_x=0, offset_mag_y=0, offset_mag_degree=0)
        gpsrunner = Gpsrunner(goal_lat=40.900522, goal_lon=-119.07909722,  # Gpsrunner(Class)のインスタンスを作成。
                              radius_Earth=6378137., THRESHOLD=15, distance_THR=1.2, pitch_time=1)
        accstack = Accstack(ygradlist=[0, 0, 0, 0, 0, 0],  # Accstack(Class)のインスタンスを作成。
                            startstack_THR=15, finishstack_THR=10, turnover_THR=-5, pitch_time=30, ygradoffset=6)
        gpsstack = Gpsstack(GPS_stack_radius=3, latlist=[200, 300, 400, 500], lonlist=[  # Gpsstack(Class)のインスタンスを作成。
                            200, 300, 400, 500], latrate=111015.4872, lonrate=89925.9685, pitch_time=60)
        stackrun = Stackrun()  # Stackrun(Class)のインスタンスを作成。
        camerarun = Camerarun(resolution=(512, 384), framerate=10,  # Camerarun(Class)のインスタンスを作成。
                              occ_THR_low=0.005, occ_THR_high=0.1, range_THR=200, pt_time=5)
        motor = Motor()  # Motor(Class)のインスタンスを作成。

        while True:
            if int(longsleep.cd_time) <= int(longsleep.com_time):  # com_timeをcd_timeが下回るときにbreakする。
                break
            runpattern.sign_on()  # LEDの操作。longsleep.pt_timeは LEDが点滅する時間*2 & 判定のループインターバル。
            sleep(longsleep.pt_time/2)
            runpattern.sign_off()
            sleep(longsleep.pt_time/2)

            # 1ループ後からlongsleep.pt_timeを超えたらカウントダウンが更新される。
            if step.evaluate_longsleep_steptime().seconds >= longsleep.pt_time:  # 1ループでpt_timeを超えるとcd_timeを更新する(ifは予防線)。
                longsleep.set()  # txtを通してtt_timeを更新する。
                longsleep.rewrite()  # txtの値を更新。
                print(longsleep.cd_time)
                step.set_longsleep_steptime()  # txtからスリープタイムの値を受け取る。

        communication.start()  # 通信開始。

        while True:
            if int(longsleep.cd_time) <= int(longsleep.ld_time):  # ld_timeをcd_timeが下回るときにbreakする。(ld_timeを0とするとわかりやすい)
                break
            if step.evaluate_longsleep_steptime().seconds >= longsleep.pt_time:
                longsleep.set()
                longsleep.rewrite()
                print(longsleep.cd_time)
                step.set_longsleep_steptime()

        step.set_landing_steptime()  # ここから着地判定を始める。

        while True:
            if int(longsleep.cd_time) <= -1:  # longsleepタイムを過ぎた場合は着地をスキップ。
                break
            else:
                if step.evaluate_landing_steptime().seconds + step.evaluate_landing_steptime().microseconds/1000000 > 0.5:  # 0.5秒ごとに判定を行う。
                    landingdetect.set()
                    landingdetect.detect()  # 着地を判定。着地したと判定すると landingdetect.detectsign = 1 を代入。
                    landingdetect.measureprint()
                    step.set_landing_steptime()
                if step.evaluate_longsleep_steptime().seconds >= longsleep.pt_time:
                    longsleep.set()
                    longsleep.rewrite()
                    print(longsleep.cd_time)
                    step.set_longsleep_steptime()
                if landingdetect.detectsign == 1 or longsleep.cd_time == 0:  # 着地判定をした、もしくはcd_timeが0になった場合、エンベロープ展開を行う。
                    landingdetect.warning()
                    landingdetect.nicrburn()
                    print("start burning")
                    sleep(5)
                    landingdetect.finish_run(runtime=5)
                    print("open")
                    runpattern.stop()
                    break

        longsleep.cd_time = -1  # 再起動したらburningの工程を無視して進む。
        longsleep.rewrite()

        while True:  # GPS走行と画像処理走行を繰り返すフェーズ。画像処理走行はゴールから離れすぎたときGPSのフェーズに戻る。
            step.set_gpsrun_steptime()  # それぞれの時間を初期化。各ループに入るための変数。
            step.set_gpsstack_steptime()
            step.set_accstack_steptime()

            while True:
                print("start GPSrun")
                sensor.set_gps()  # gps, 9軸, 加速度の値をそれぞれ取得。
                sensor.set_mag()
                sensor.set_acc()
                gpsrunner.set(sensor)  # センサーの値をgpsrunnerのインスタンスに入力。
                gpsrunner.gpsrun_print()
                if gpsrunner.distance_ntg <= gpsrunner.distance_THR:  # GPS走行で近距離まで近づけたか判断。
                    gpsrunner.gpsrunfinish()
                    break
                if step.evaluate_gpsrun_steptime().seconds >= gpsrunner.pitch_time:
                    gpsrunner.gpsrun(motor)
                    logs.con_log(gpsrunner.loglist)  # 位置などのログを作成。
                    step.set_gpsrun_steptime()  # ステップタイムを更新。
                if step.evaluate_accstack_steptime().seconds+step.evaluate_accstack_steptime().microseconds/1000000 >= accstack.pitch_time:
                    accstack.set(sensor)
                    print(accstack.ygradlist)
                    print(accstack.acc_z)
                    if accstack.acc_z <= accstack.turnover_THR:  # 加速度によるスタックの判定。
                        accstack.startprint()
                        runpattern.stack(pattern=4, runtime=1)  # 一度スタックを抜けるための走行を行う。
                        sensor.set_acc()
                        accstack.set(sensor)
                        accstack.nowprint()
                        sleep(1)
                        if accstack.acc_z <= accstack.turnover_THR:  # もう一度判定。
                            while True:
                                stackrun.set(pattern_range=[
                                    12, 19], runtime_range=[1, 10])  # ランダムなパターンで走行を行う。
                                stackrun.escaperun()
                                sensor.set_acc()
                                accstack.set(sensor)
                                accstack.nowprint()
                                sleep(1)
                                if accstack.acc_z >= accstack.turnover_THR:  # スタック状態を抜けたかどうか判定。
                                    break
                    step.set_accstack_steptime()  # ステップタイムを更新。
                if step.evaluate_gpsstack_steptime().seconds >= gpsstack.pitch_time:
                    gpsstack.set(sensor)  # GPSによるスタックの判定。
                    print(gpsstack.dif_abs_m)
                    print(gpsstack.latlist)
                    if gpsstack.dif_abs_m <= gpsstack.GPS_stack_radius:
                        gpsstack.startprint()
                        while True:
                            stackrun.set(pattern_range=[
                                         1, 19], runtime_range=[2, 6])  # ランダムなパターンで走行を行う。
                            stackrun.escaperun()
                            sensor.set_gps()
                            gpsstack.set_diflist(sensor)
                            gpsstack.nowprint()
                            sleep(1)
                            if min(gpsstack.diflist) > gpsstack.GPS_stack_radius:
                                gpsstack.finishprint()
                                gpsstack.set_latlist(  # 問題のない値に初期化。
                                    latlist=[200, 300, 400, 500])
                                gpsstack.set_lonlist(  # 問題のない値に初期化。
                                    lonlist=[200, 300, 400, 500])
                                break
                    step.set_gpsstack_steptime()  # ステップタイムを更新。
                sleep(0.5)

            step.set_imagesave_steptime()  # それぞれの時間を初期化。各ループに入るための変数。
            step.set_accstack_steptime()
            step.set_error_steptime()

            while True:
                camerarun.getdata()  # カメラからデータを取得。
                camerarun.run(motor)  # 画像処理走行を行う。
                logs.cam_log(camerarun.loglist)  # ログを残す。
                if step.evaluate_imagesave_steptime().seconds >= camerarun.pt_time:
                    camerarun.save()  # 画像を保存。
                    step.set_imagesave_steptime()  # ステップタイムを更新。
                if step.evaluate_accstack_steptime().seconds >= camerarun.pt_time:
                    sensor.set_acc()  # 加速度の値を取得。
                    accstack.set(sensor)
                    if accstack.acc_z <= accstack.turnover_THR:  # 加速度によるスタックの判定。(GPSと同様)
                        accstack.startprint()
                        runpattern.stack(pattern=4, runtime=1)
                        sensor.set_acc()
                        accstack.set(sensor)
                        accstack.nowprint()
                        sleep(1)
                        if accstack.acc_z <= accstack.turnover_THR:
                            while True:
                                stackrun.set(pattern_range=[
                                    12, 19], runtime_range=[1, 10])
                                stackrun.escaperun()
                                sensor.set_acc()
                                accstack.set(sensor)
                                accstack.nowprint()
                                sleep(1)
                                if accstack.acc_z >= accstack.turnover_THR:
                                    break
                    step.set_accstack_steptime()
                if step.evaluate_error_steptime().seconds > 60:
                    sensor.set_gps()  # gpsの値を取得。
                    gpsrunner.set(sensor)
                if camerarun.jd_sign == 2 or gpsrunner.distance_ntg > gpsrunner.distance_THR:  # 画像処理走行でゴールに達したか、ゴールから離れすぎた場合break。
                    break

            if camerarun.jd_sign == 2:  # ゴールに達したと判断した場合break。
                break

            else:  # ゴールから離れすぎた場合、GPS走行から開始。
                pass

        gps_setting_socket.close()

        while True:  # 終了。
            sleep(10)

    except KeyboardInterrupt:
        longsleep.cd_time = longsleep.fr_time
        longsleep.rewrite()


while True:
    try:
        main()
        break
    except KeyboardInterrupt:
        runpattern.stop()
        GPIO.cleanup()
    except:
        pass

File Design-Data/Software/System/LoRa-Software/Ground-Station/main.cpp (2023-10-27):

#include "mbed.h"
#include "FUSiON_RM92A.h"

Serial pc(USBTX, USBRX, 115200);
Serial rm_serial(D1, D0, 115200);

RM92 rm(rm_serial);

void downlink_handler(char* data);

char mission_timer_reset;
short mission_time_init;
float mission_time;
float flight_time;
char flags;
char flags2;

float lat10000;
float lon10000;
float press1;
float temp1;
float press2;
float temp2;
float alt;
float press;
float temp;
int phase;

int main(){
    while(1){
        rm.attach(downlink_handler);
        if(pc.readable()){
            char cmd[1];
            cmd[0] = pc.getc();
            rm.send_cmd(0x0000, cmd);
            pc.printf("send:\t%x\r\n", cmd[0]);
        }
    }  
    }




void downlink_handler(char* data){  
    press = (float(data[7]) * 256 + float(data[8])) / 10;
    temp = (float(data[9]) * 256 + float(data[10])) / 100;
    lat10000 = (float(data[11]) * 10000 + float(data[12]) * 100 + float(data[13])) / 10000;
    lon10000 = (float(data[14]) * 10000 + float(data[15]) * 100 + float(data[16])) / 10000;
    phase = int(data[17]);

    pc.printf(" LAT:\t\t%.6f\r\n", lat10000);
    pc.printf(" LON:\t\t%.6f\r\n", lon10000);
    pc.printf(" PRESS:\t\t%.2f[hPa]\r\n", press);
    pc.printf(" TEMPERATURE:\t%.2f[C]\r\n", temp);
    pc.printf("\r\n");
    
  
}

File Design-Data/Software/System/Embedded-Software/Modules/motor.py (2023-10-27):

import runpattern as motor


class Motor:  # 初期設定を行うメソッド。
    def __init__(self):
        self.lefttimes = 0
        self.righttimes = 0
        pass

    def left(self):  # 前進してから左に回る走行を行うメソッド。
        motor.forward(0.02*(self.lefttimes % 11))
        motor.leftturn(0.2-0.02*(self.lefttimes % 11))
        self.lefttimes = self.lefttimes + 1

    def right(self):  # 前進してから右に回る走行を行うメソッド。
        motor.forward(0.02*(self.lefttimes % 11))
        motor.rightturn(0.2-0.02*(self.lefttimes % 11))
        self.righttimes = self.righttimes + 1

    def forward_gps(self):  # 前進するメソッド。
        self.lefttimes = 0
        self.righttimes = 0
        motor.forward()

    def forward_cam(self):  # 後退するメソッド。
        self.lefttimes = 0
        self.righttimes = 0
        motor.forward(0.2)

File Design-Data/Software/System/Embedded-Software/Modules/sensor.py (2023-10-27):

import math
import json


class Sensor:
    def __init__(self, i2c, sensor, gps_socket, data_stream, lastval, offset_mag_x, offset_mag_y, offset_mag_degree):  # 初期設定を行うメソッド。
        self.i2c = i2c
        self.sensor = sensor
        self.gps_socket = gps_socket
        self.data_stream = data_stream
        self.lastval = lastval
        self.offset_mag_x = offset_mag_x
        self.offset_mag_y = offset_mag_y
        self.offset_mag_degree = offset_mag_degree

    def set_gps(self):  # gpsの値をインスタンスのメンバに代入するメソッド。
        self.lat, self.lon = self.gpsget()

    def set_mag(self):  # 地磁気の値をインスタンスのメンバに代入するメソッド。
        self.mag_x, self.mag_y, self.mag_z = self.getmag()

    def set_acc(self):  # 重力加速度の値をインスタンスのメンバに代入するメソッド。
        self.acc_x, self.acc_y, self.acc_z = self.getacc()

    def gpsget(self):  # GPSの値を取得するメソッド。
        try:
            gps_dict = {
                "time": "n/a",
                "lat": "n/a",
                "lon": "n/a",
            }
            for new_data in self.gps_socket:
                if not new_data:
                    continue

                new_data_dict = json.loads(new_data)
                if new_data_dict["class"] != "TPV":
                    continue

                # ref: https://github.com/wadda/gps3/blob/master/gps3/gps3.py
                self.data_stream.unpack(new_data)
                if self.data_stream.TPV["time"] == "n/a":
                    continue

                gps_dict = {
                    "time": self.data_stream.TPV["time"],
                    "lat": self.data_stream.TPV["lat"],
                    "lon": self.data_stream.TPV["lon"],
                }
                break

            lat_i = gps_dict["lat"]
            lon_i = gps_dict["lon"]
            return (lat_i, lon_i)

        except:
            lat_i = 0
            lon_i = 0
            return (lat_i, lon_i)

    def getmag(self):  # 地磁気の値を取得するメソッド。
        [mag_x, mag_y, mag_z] = self.sensor.magnetic
        mag_x = mag_x - self.offset_mag_x
        mag_y = mag_y - self.offset_mag_y
        return (mag_x, mag_y, mag_z)

    def getacc(self):  # 加速度の値を取得するメソッド。
        [accel_x, accel_y, accel_z] = self.sensor.acceleration
        return (accel_x, accel_y, accel_z)

    def rad_magnet(self):  # 地磁気方向を取得するメソッド。
        rad = math.atan2(self.mag_y, self.mag_x)
        return rad

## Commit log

2023-06-13 組み込み統合プロブラムとその説明文を追加した。
2023-06-13 組み込みプログラムとその説明文を追加した。
2023-06-13 モータの動作プログラムを作成した
2023-06-13 モータードライバー用のテストプログラムの作製
2023-06-13 Delete Design-Data/Software/Component-Test/MotorDriver directory
    ごめんなさい．プッシュする先間違えたので削除します
2023-06-19 9軸と気圧を追加
2023-06-19 READMEの追加
2023-06-19 回路図データアップロード
    [EDI2CAP.CFG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]
2023-06-25 メインのコメントアウトを加えました。
2023-06-25 Cadデータをパーツに分けて追加した。
    [GYSFDMAXB.f3d, bearingholder.f3d, coupling.f3d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]
2023-07-31 GPSの追加
2023-08-01 コメントアウトを加えました。 部品の購入リンクやデータシートをまとめました。
2023-08-01 CanSatの組み上げ書類を作成しました．
2023-08-07 rm92a追加
2023-08-14 軽微修正
2023-08-15 ファイル整理done
    [arliss-B_Cu.gbl, arliss-B_Mask.gbs, arliss-B_Paste.gbp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]
2023-08-21 組み上げ書の更新(pdf化，md，画像の削除)
2023-08-21 motor.pyを修正しました
2023-08-28 パラコード,畳み方についての記述追加
2023-08-30 RM92Aまわりについて記入
2023-08-30 最終修正(確認必要)
2023-08-30 最終修正(確認必要2)
2023-08-30 最終修正(画像サイズ調整)
2023-09-06 無線について追加
    無線について追加
2023-09-06 エンベロープ作成方法記載
2023-09-06 CanSat組み上げ書に配線部分を追加した
2023-09-06 Operation-Control; Fix indention added
    改行されていない部分の改行を行なった
2023-09-11 エンベロープ作成方法記載2
2023-09-11 エンベロープ作成方法記載3
2023-09-12 MD 画像追加の確認
2023-09-12 画像の確認
2023-09-12 画像の追加
2023-09-12 dev-m2-ob: update エンベロープの作成方法について加筆しました
2023-09-12 RM92A: Fix images added
    [main.cpp]
2023-09-13 dev-m2-ob: fix 挿絵・文言など修正
2023-09-25 all: sort out
    [GYSFDMAXB.f3d, bearingholder.f3d, coupling.f3d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]
2023-09-27 Envelope: Fix expression
    エンベロープの文章の中で誤った情報や
    誤字があったので修正しました。
